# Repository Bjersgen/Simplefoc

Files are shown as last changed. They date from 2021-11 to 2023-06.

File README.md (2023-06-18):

# Simplefoc
Update 2023.3.9:

Firstly, there are some facts that need to be clarified, which I was not aware of when I initially started this project. Although the performance of these PCBs is normal at low speeds. After repeated verification, it was found that the project based on ESP32 can only reach a speed of 1000RPM when running a BLDC motor with an internal resistance of 1.5 ohms. When the speed continues to increase, the motor will exhibit symptoms such as jitter, increased current, reduced efficiency, and heat generation. This is due to several reasons working together.

1、The code of SimpleFOC platform itself has certain limitations. Because SimpleFOC is based on platforms such as Arduino, the core of the code, which is the SVPWM part, is placed in the main loop. This causes the waveform of the final output of the three phases to become stair-shaped when the speed is too high, and the processing frequency of the MCU cannot guarantee a sinusoidal waveform.

2、Do not use I2C communication for the AS5600 encoder as it is slow to trigger and has a delay, and the communication frequency has a great impact on the main loop of FOC.

3、Esp32 or Arduino itself does not have powerful features such as interrupts and DMA like stm32, and adding these functions to the underlying code of SimpleFOC is also difficult.

To address the issue of FOC being unable to run at high speeds, the following improvement solutions are recommended:

1、Change the encoder to AS5047 and use SPI or PWM, paying attention to signal integrity.

2、Use stm32 series as the main control MCU, utilize interrupts to process the SVPWM part, and trigger the interrupt every time the encoder's reading is obtained to process the direction and positioning of the magnetic field, which can greatly improve the robustness of motor control.

Feature——MAX_120W(24V*5A)——Faster(1KHZ for closed loop)

           SimpleFOC——
                            | ——BLDCmotor(self made DIY motor)
                            | ——Documents
                            | ——STM32H7_FOC
                                 |——circle(PCBs & libraries)
                            		  |——Shell(a PCB shell)
                                 |——code(using Keil5 & STM32CubeMX)
                            		  |——Inc
                            		  |——Src
                            		  |——Drivers
                            		  |——MDK-ARM
                                 |——datasheet(ICs datasheets)
                                 |——image
                                 |——readme
                            | ——pico(basic demo)                 
                            | ——pico-drv8313
                            | ——pico-drv8313 with foc
                            | ——readme

Most projects are based on Arduino, esp32-pico D4 and one project is based on stm32h743.

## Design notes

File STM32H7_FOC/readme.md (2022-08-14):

2021.12.06

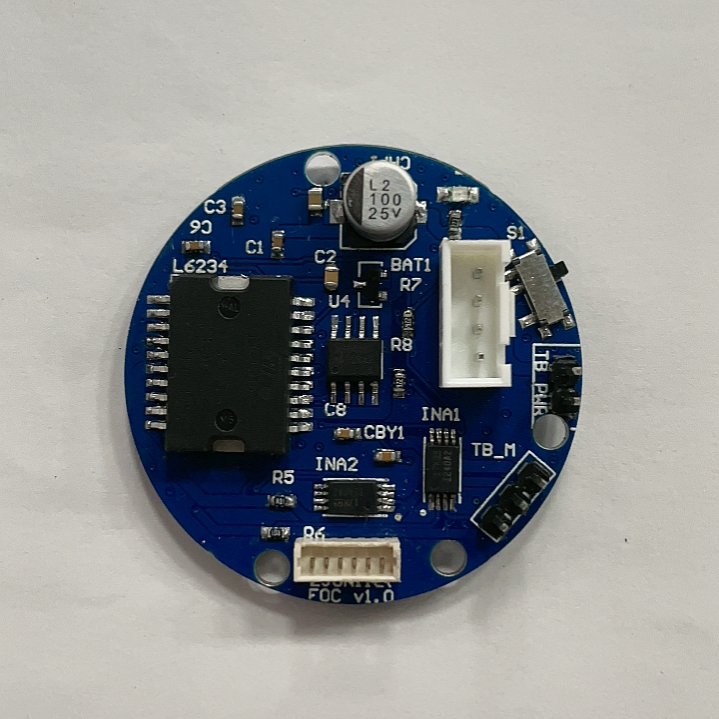
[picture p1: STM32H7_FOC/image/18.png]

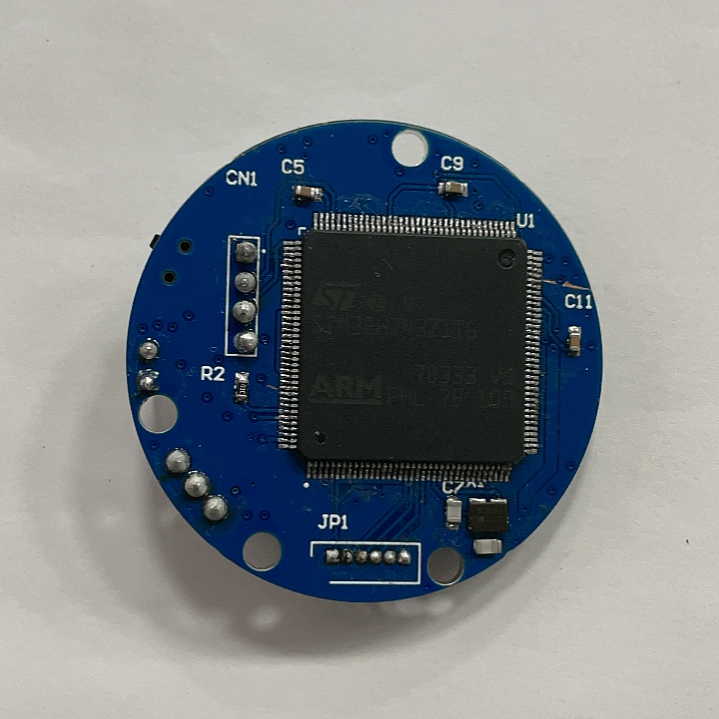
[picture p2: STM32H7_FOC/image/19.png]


基于STM32CubeMX的HAL库开发的代码

circle是基于STM32H743开发的一体化伺服系统，包括主控芯片（STM32H743）、驱动芯片、电流采样、编码器等等，对外保留了SPI接口、12-24V的供电口
以及基于SWD的调试/代码上传口、除了circle的工程外，其余的文件都是调用过的库

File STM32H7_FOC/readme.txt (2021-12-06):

2021.12.06

基于STM32CubeMX的HAL库开发的代码，目前只进行过开环测试

circle是基于STM32H743开发的一体化伺服系统，包括主控芯片（STM32H743）、驱动芯片、电流采样、编码器等等，对外保留了SPI接口、12-24V的供电口
以及基于SWD的调试/代码上传口、除了circle的工程外，其余的文件都是调用过的库

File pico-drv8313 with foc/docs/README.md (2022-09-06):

Output for 72W motor control:

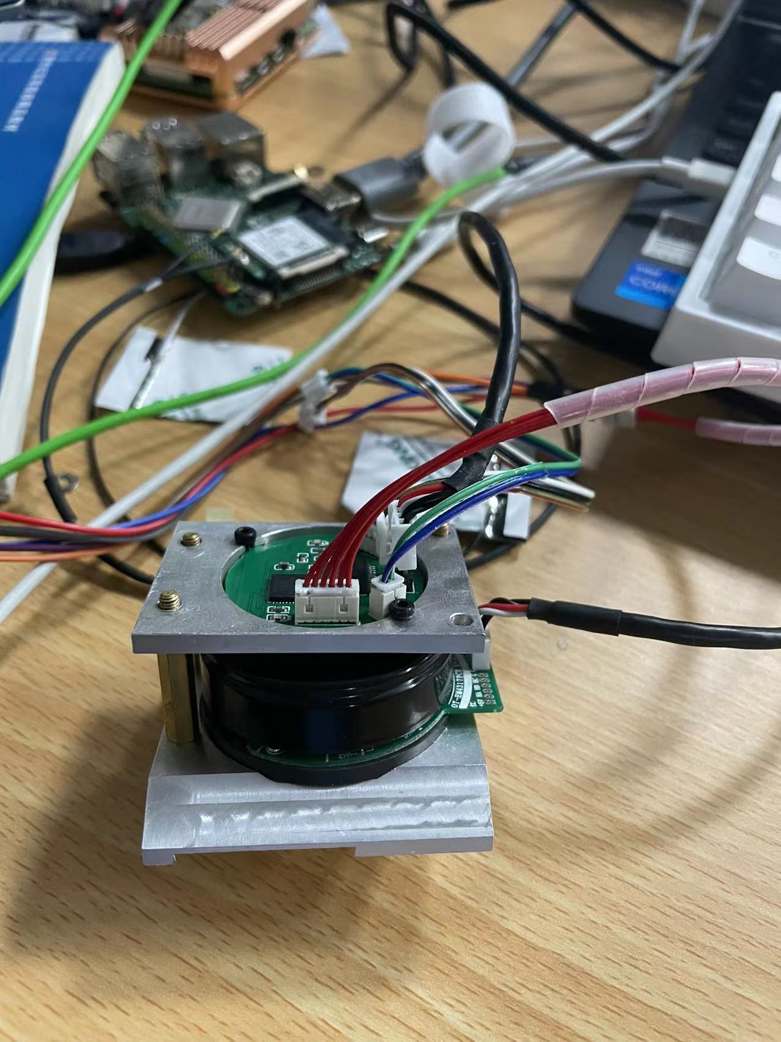
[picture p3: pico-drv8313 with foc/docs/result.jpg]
result


This directory is intended for PlatformIO Unit Testing and project tests.

Unit Testing is a software testing method by which individual units of
source code, sets of one or more MCU program modules together with associated
control data, usage procedures, and operating procedures, are tested to
determine whether they are fit for use. Unit testing finds problems early
in the development cycle.

More information about PlatformIO Unit Testing:
- https://docs.platformio.org/page/plus/unit-testing.html

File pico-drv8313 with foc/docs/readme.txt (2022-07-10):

如果是从库管理器中直接下载的SimpleFOC库需要对文件/.pio/libdeps/src/drivers/hardware_specific/esp32_mcu.cpp进行替换
文件放在该目录下，文件名为esp32_mcu.cpp

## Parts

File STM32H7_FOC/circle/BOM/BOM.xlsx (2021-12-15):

ID | Name | Designator | Footprint | Quantity | Manufacturer Part | Manufacturer | Supplier | Supplier Part | Prince
1 | 100μF | C1 | C0805 | 1
2 | 10nF | C2 | C0805 | 1
3 | 1μF | C3 | C0805 | 1
4 | 220nF | C4 | C0805 | 1
5 | 0.1μF | CBY1 | C0805 | 1
6 | 100nF | C8 | C0603 | 1
7 | 0.1μF | CL1 | C0603 | 1
8 | 1μF | C9 | C0603 | 1
9 | 100μF | CAP1 | EEH-ZA1E101XP | 1
10 | L78M08 | L1 | L7805 | 1
11 | AS5600 | U4 | SOIC8 | 1
12 | INA240A2 | INA1,INA2 | INA240 | 2
13 | STM32H743ZIT6u | U1 | LOFP100_0R5_SKT | 1
14 | Terminal connector 2pin 5mm pitch | TB_PWR | TB002-500-02BE | 1
15 | Terminal connector 3pin 5mm pitch | TB_M | 10.7MHZ | 1
16 | LED | D1 | D0805+ | 3
17 | 4 pin male header long | CN1 | HDR_1*4_2R54_V_M | 1
18 | 6 pin male header long | JP1 | HDR_1*6_2R54_V_M | 1
19 | solder_connection | SCT1 | solder_connection | 1
20 | solder_connectiong | SCT10 | solder_connection_tripple | 1
21 | 10mOhm | R5 | R/C0603 | 1
22 | 10mOhm | R6 | R/C0603 | 1
23 | 4.7KOhm | R7 | 0603R | 1
24 | 4.7KOhm | R8 | 0603R | 1

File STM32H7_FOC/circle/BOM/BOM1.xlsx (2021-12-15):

Name | Footprint | Quantity
100μF | C0805 | 5
10nF | C0805 | 5
1μF | C0805 | 5
220nF | C0805 | 5
0.1μF | C0805 | 5
100nF | C0603 | 5
0.1μF | C0603 | 5
1μF | C0603 | 5
100μF | EEH-ZA1E101XP | 5
L78M08 | L7805 | 5
AS5600 | SOIC8 | 5
INA240A2 | INA240 | 10
STM32H743ZIT6 | LOFP144_0R5_SKT | 5
Terminal connector 2pin 5mm pitch | TB002-500-02BE | 5
Terminal connector 3pin 5mm pitch | 10.7MHZ | 5
LED | D0805+ | 5
4 pin male header long | HDR_1*4_2R54_V_M | 5
6 pin male header long | HDR_1*6_2R54_V_M | 5
solder_connection | solder_connection | 5
solder_connectiong | solder_connection_tripple | 5
10mOhm | R/C0603 | 10
4.7KOhm | 0603R | 10

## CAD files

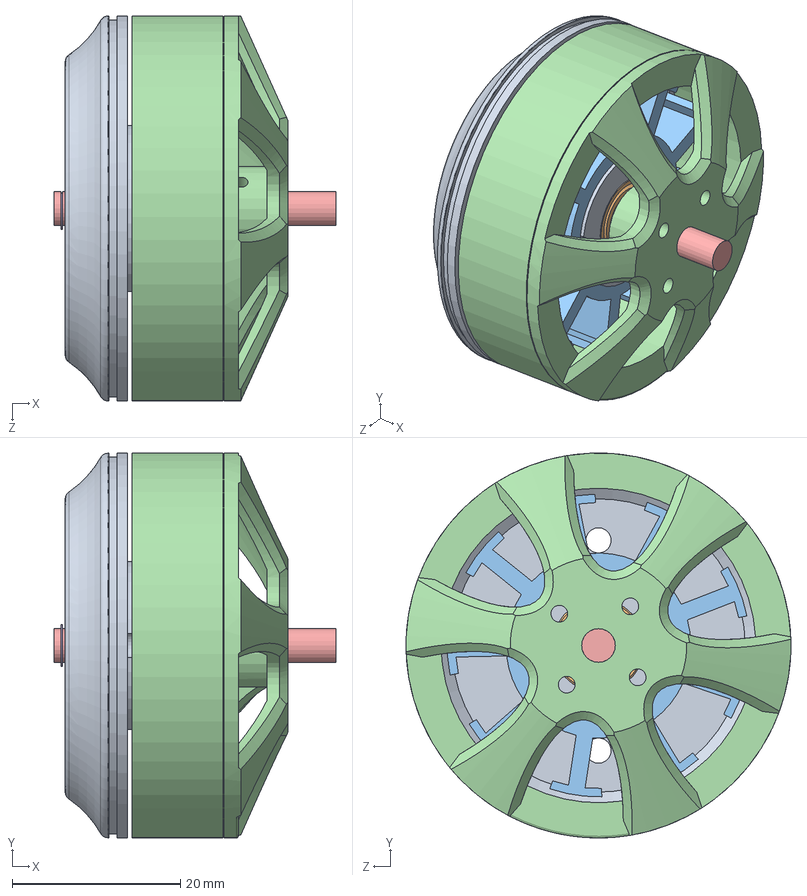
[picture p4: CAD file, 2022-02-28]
BLDCmotor/电机.SLDASM
33.5 x 45.8 x 45.8 mm
R1140ZZ bearing x 2
axle
circlip

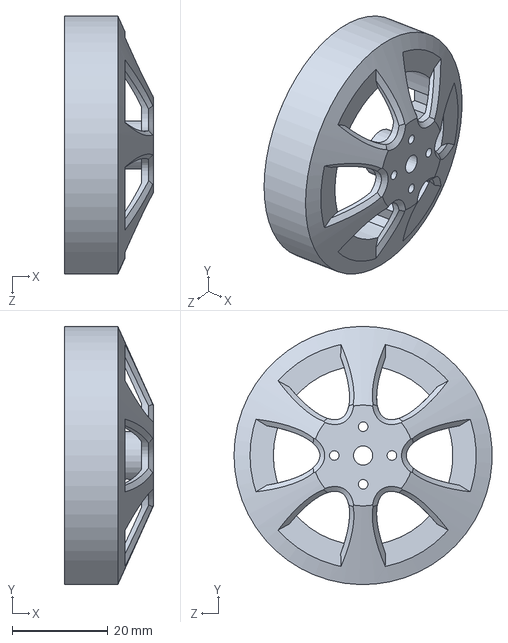
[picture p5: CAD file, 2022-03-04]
BLDCmotor/外转子.SLDPRT
18.5 x 53.8 x 53.8 mm

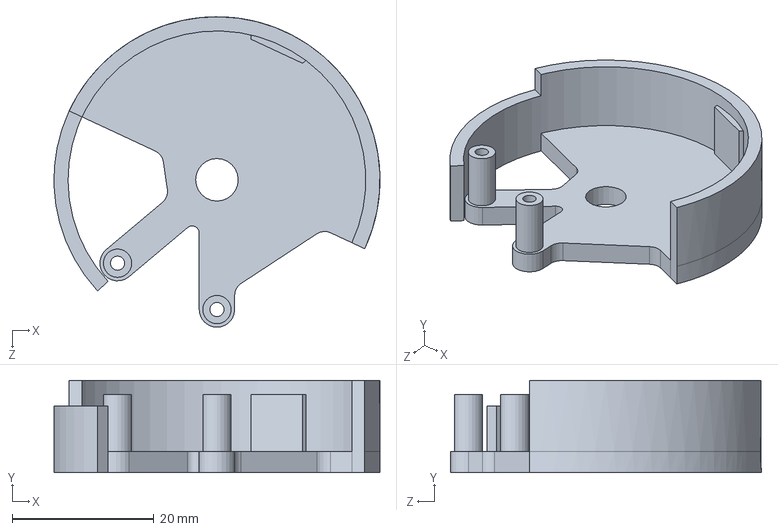
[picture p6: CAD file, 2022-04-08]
STM32H7_FOC/circle/Solidworks shell/shell.SLDPRT
46.0 x 13.0 x 43.8 mm

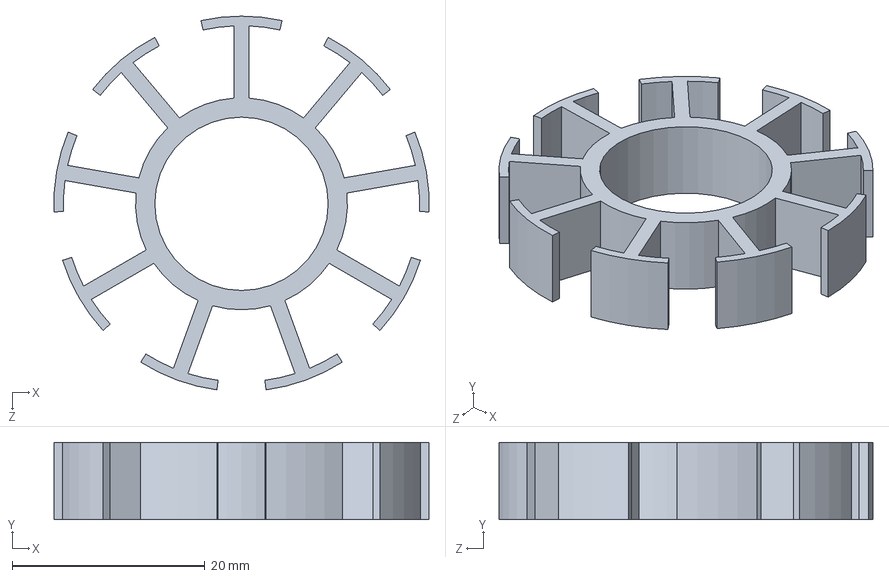
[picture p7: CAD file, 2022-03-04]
BLDCmotor/内定子.SLDPRT
38.9 x 8.00 x 38.8 mm

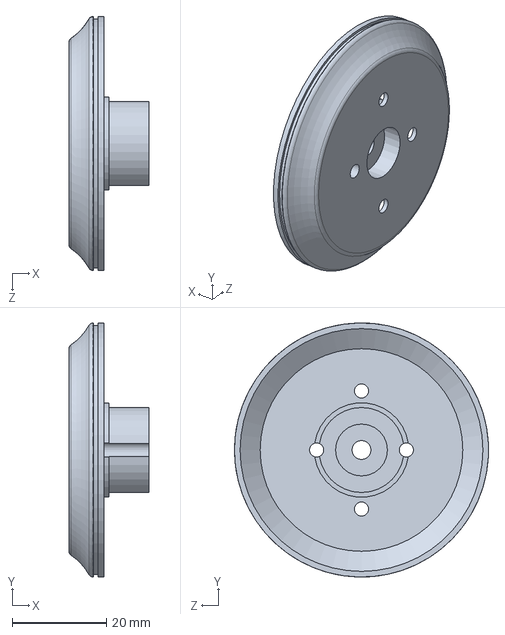
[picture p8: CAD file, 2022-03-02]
BLDCmotor/底座.SLDPRT
17.0 x 53.8 x 53.8 mm

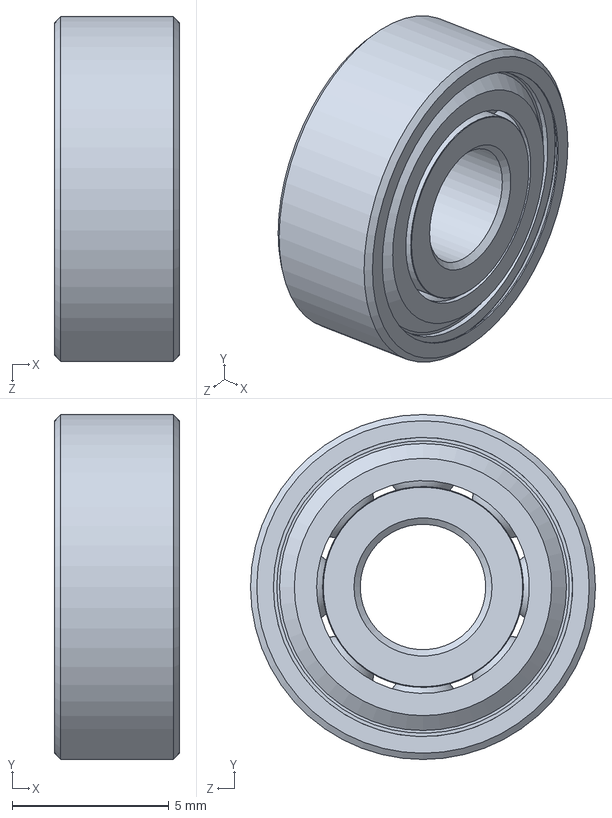
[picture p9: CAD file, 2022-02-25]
BLDCmotor/轴承.SLDPRT
4.00 x 11.0 x 11.0 mm

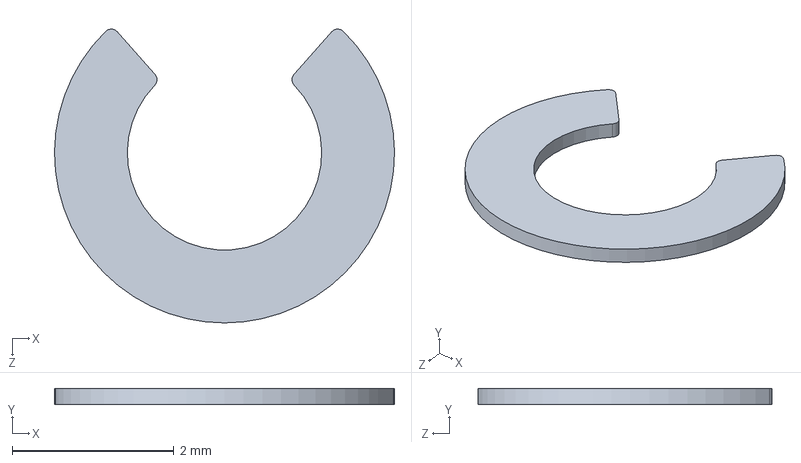
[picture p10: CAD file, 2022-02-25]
BLDCmotor/circlip.SLDPRT
4.20 x 0.2 x 3.63 mm

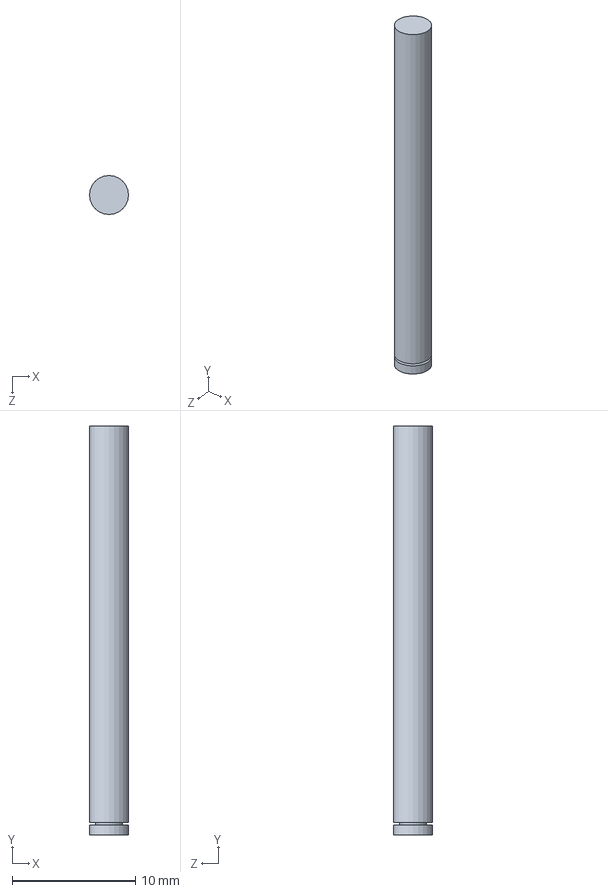
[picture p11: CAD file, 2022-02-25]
BLDCmotor/光轴.SLDPRT
3.17 x 33.2 x 3.17 mm

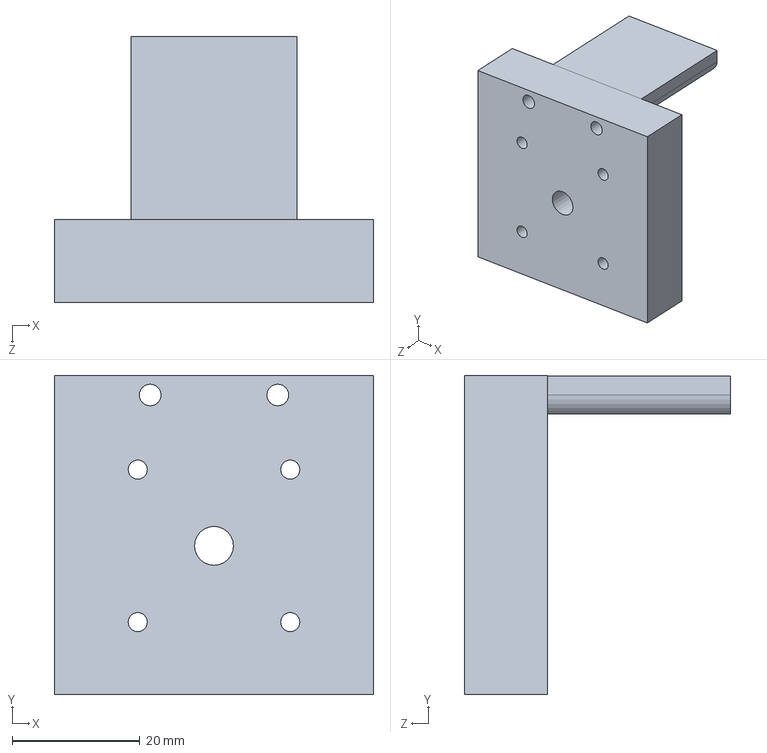
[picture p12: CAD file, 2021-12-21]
BLDCmotor/base.SLDPRT
50.0 x 50.0 x 41.7 mm

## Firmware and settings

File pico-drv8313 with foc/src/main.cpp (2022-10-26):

#include <Arduino.h>
#include <SimpleFOC.h>
#include "Wire.h"
//设置I2C设备地址，每个电机设置一个地址
#define I2C_DEV_ADDR 0x31
//电机转速
String target_velocity_string;
int target_velocity = 0;
//主机请求回复
void onRequest(){
  Wire1.print(target_velocity);
  //Serial.println("HaveRequest");
}
//收包中断，收到速度修改电机转动速度
void onReceive(int len){
  //Serial.printf("Receive[%d]: ", len);
  while(Wire1.available()){
    target_velocity_string = Wire1.read();
    target_velocity = target_velocity_string.toInt();
    if(target_velocity>=128) target_velocity = target_velocity - 256;
  }
}

//编码器采用I2C通信
MagneticSensorI2C sensor = MagneticSensorI2C(AS5600_I2C);
//电机极对数
BLDCMotor motor = BLDCMotor(8);
// BLDCDriver3PWM driver = BLDCDriver3PWM(pwmA, pwmB, pwmC, Enable(optional));
BLDCDriver3PWM driver = BLDCDriver3PWM(19, 21, 22, 23);


void setup() {
  pinMode(32, OUTPUT);
  pinMode(33, INPUT);
  pinMode(34, OUTPUT);
  digitalWrite(32,HIGH);
  digitalWrite(34,HIGH);
  Serial.begin(115200);
  //检查各个部分是否正确
  Serial.setDebugOutput(true);
  Wire1.onReceive(onReceive);
  Wire1.onRequest(onRequest);
  //与主机进行通信的I2C引脚
  Wire1.begin((uint8_t)I2C_DEV_ADDR,13,15);


  motor.useMonitoring(Serial);
  //与编码器通信的I2C引脚
  Wire.setPins(25,26);
  Wire.setClock(400000);
  sensor.init();
  motor.linkSensor(&sensor);
  //供电电压
  driver.voltage_power_supply = 16.8;
  driver.init();
  motor.linkDriver(&driver);
  motor.voltage_limit = 3;   // [V]
  motor.controller = MotionControlType::velocity;
  //PID参数
  motor.PID_velocity.P = 0.1;
  motor.PID_velocity.I = 2;
  motor.PID_velocity.D = 0;
  motor.PID_velocity.output_ramp = 1000;
  motor.LPF_velocity.Tf = 0.01;
  motor.init();
  motor.initFOC();
  motor.monitor_variables = _MON_ANGLE; // default _MON_TARGET | _MON_VOLT_Q | _MON_VEL | _MON_ANGLE
  _delay(1000);

  // #if CONFIG_IDF_TARGET_ESP32
  // char message[64];
  // snprintf(message, 64, "%u Packets.", target_velocity);
  // Wire1.slaveWrite((uint8_t *)message, strlen(message));
  // #endif
  Serial.print(1);
}

void loop() {
  //闭环速度控制
  motor.loopFOC();
  motor.move(target_velocity);
  
  if(sensor.getVelocity()>3){
    motor.voltage_limit = 16.5;
  }
  // Serial.println(target_velocity);
  // motor.monitor();
  Serial.print(sensor.getAngle());
  Serial.print("\t");
  Serial.println(sensor.getVelocity());
  Serial.print(digitalRead(33));
  
}

// #include <Arduino.h>
// #include <SimpleFOC.h>
// #include "Wire.h"
// //设置I2C设备地址，每个电机设置一个地址
// #define I2C_DEV_ADDR 0x30
// //电机转速
// String target_velocity_string;
// int target_velocity = 0;
// //主机请求回复
// void onRequest(){
//   Wire1.print(target_velocity);
//   //Serial.println("HaveRequest");
// }
// //收包中断，收到速度修改电机转动速度
// void onReceive(int len){
//   //Serial.printf("Receive[%d]: ", len);
//   while(Wire1.available()){
//     target_velocity_string = Wire1.read();
//     target_velocity = target_velocity_string.toInt();
//     if(target_velocity>=128) target_velocity = target_velocity - 256;
//   }
// }
// //电机极对数
// BLDCMotor motor = BLDCMotor(8);
// // BLDCDriver3PWM driver = BLDCDriver3PWM(pwmA, pwmB, pwmC, Enable(optional));
// BLDCDriver3PWM driver = BLDCDriver3PWM(19, 21, 22, 23);


// void setup() {

//   pinMode(32, OUTPUT);
//   pinMode(33, INPUT);
//   pinMode(34, OUTPUT);
//   digitalWrite(32,HIGH);
//   digitalWrite(34,HIGH);
//   Serial.begin(115200);
//   //检查各个部分是否正确
//   Serial.setDebugOutput(true);
//   Wire1.onReceive(onReceive);
//   Wire1.onRequest(onRequest);
//   //与主机进行通信的I2C引脚
//   Wire1.begin((uint8_t)I2C_DEV_ADDR,13,15);


//   motor.useMonitoring(Serial);
//   //与编码器通信的I2C引脚
//   Wire.setPins(25,26);
//   Wire.setClock(400000);
//   //供电电压
//   driver.voltage_power_supply = 16.8;
//   driver.init();
//   motor.linkDriver(&driver);
//   motor.voltage_limit = 3;   // [V]
//   motor.controller = MotionControlType::velocity_openloop;

//   motor.init();
//   motor.monitor_variables = _MON_ANGLE; // default _MON_TARGET | _MON_VOLT_Q | _MON_VEL | _MON_ANGLE
//   _delay(1000);

//   // #if CONFIG_IDF_TARGET_ESP32
//   // char message[64];
//   // snprintf(message, 64, "%u Packets.", target_velocity);
//   // Wire1.slaveWrite((uint8_t *)message, strlen(message));
//   // #endif
//   Serial.print(1);
// }

// void loop() {
//   //闭环速度控制
//   motor.move(target_velocity);
  
//   // Serial.println(target_velocity);
//   // motor.monitor();
//   Serial.print(digitalRead(33));
  
// }

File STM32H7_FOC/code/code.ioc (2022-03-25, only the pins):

Mcu.UserName=STM32H743ZITx
PA1.GPIO_Label=RMII_REF_CLK
PA1.Signal=ETH_REF_CLK
PA10.GPIO_Label=USB_ID
PA10.Signal=USB_OTG_FS_ID
PA11.GPIO_Label=USB_DM
PA11.Signal=USB_OTG_FS_DM
PA12.GPIO_Label=USB_DP
PA12.Signal=USB_OTG_FS_DP
PA2.GPIO_Label=RMII_MDIO
PA2.Signal=ETH_MDIO
PA3.Signal=USART2_RX
PA7.GPIO_Label=RMII_CRS_DV
PA7.Signal=ETH_CRS_DV
PA8.GPIO_Label=USB_SOF [TP1]
PA8.Signal=USB_OTG_FS_SOF
PA9.GPIO_Label=USB_VBUS
PA9.Signal=USB_OTG_FS_VBUS
PB13.GPIO_Label=RMII_TXD1
PB13.Signal=ETH_TXD1
PB14.GPIO_Label=LD3 [Red]
PB14.Signal=GPIO_Output
PB7.GPIO_Label=LD2 [Blue]
PB7.Signal=GPIO_Output
PC1.GPIO_Label=RMII_MDC
PC1.Signal=ETH_MDC
PC13.GPIO_Label=USER_Btn [B1]
PC13.Signal=GPXTI13
PC4.GPIO_Label=RMII_RXD0
PC4.Signal=ETH_RXD0
PC5.GPIO_Label=RMII_RXD1
PC5.Signal=ETH_RXD1
PD5.Signal=USART2_TX
PD8.GPIO_Label=STLK_RX [STM32F103CBT6_PA3]
PD8.Signal=USART3_TX
PD9.GPIO_Label=STLK_TX [STM32F103CBT6_PA2]
PD9.Signal=USART3_RX
PE11.Signal=S_TIM1_CH2
PE13.Signal=S_TIM1_CH3
PE9.Signal=S_TIM1_CH1
PG11.GPIO_Label=RMII_TX_EN
PG11.Signal=ETH_TX_EN
PG13.GPIO_Label=RMII_TXD0
PG13.Signal=ETH_TXD0
PG6.GPIO_Label=USB_PowerSwitchOn [STMPS2151STR_EN]
PG6.Signal=GPIO_Output
PG7.GPIO_Label=USB_OverCurrent [STMPS2151STR_FAULT]
PG7.Signal=GPIO_Input

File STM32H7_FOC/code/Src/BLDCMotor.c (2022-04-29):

#include "MyProject.h"
#include "stdio.h"



/******************************************************************************/
extern float target;
/******************************************************************************/
long sensor_direction;
float voltage_power_supply;
float voltage_limit;
float voltage_sensor_align;
int  pole_pairs;
unsigned long open_loop_timestamp;
float velocity_limit;
float current_limit;
/******************************************************************************/
int alignSensor(void);
float velocityOpenloop(float target_velocity);
float angleOpenloop(float target_angle);

/******************************************************************************/
void Motor_init(void)
{
	printf("MOT: Init\r\n");
	
//	new_voltage_limit = current_limit * phase_resistance;
//	voltage_limit = new_voltage_limit < voltage_limit ? new_voltage_limit : voltage_limit;
	if(voltage_sensor_align > voltage_limit) voltage_sensor_align = voltage_limit;
	
	pole_pairs=7;
	sensor_direction=UNKNOWN;
	
	M1_Enable;
	printf("MOT: Enable driver.\r\n");
}

void Motor_initFOC(void)
{
	alignSensor();    
	
	//added the shaft_angle update
	//angle_prev=getAngle();  //getVelocity(),make sure velocity=0 after power on
	HAL_Delay(50);
	shaft_velocity = shaftVelocity();  //
	HAL_Delay(5);
	shaft_angle = shaftAngle();// shaft angle
	if(controller==Type_angle)target=shaft_angle;//
	
	HAL_Delay(200);
}

int alignSensor(void)
{
	long i;
	float angle;
	float mid_angle,end_angle;
	float moved;
	
	printf("MOT: Align sensor.\r\n");
	
	// find natural direction
	// move one electrical revolution forward
	for(i=0; i<=500; i++)
	{
		angle = _3PI_2 + _2PI * i / 500.0;
		setPhaseVoltage(voltage_sensor_align, 0,  angle);
		HAL_Delay(2);
	}
	mid_angle=getAngle();
	
	for(i=500; i>=0; i--) 
	{
		angle = _3PI_2 + _2PI * i / 500.0 ;
		setPhaseVoltage(voltage_sensor_align, 0,  angle);
		HAL_Delay(2);
	}
	end_angle=getAngle();
	setPhaseVoltage(0, 0, 0);
	HAL_Delay(200);
	
	printf("mid_angle=%.4f\r\n",mid_angle);
	printf("end_angle=%.4f\r\n",end_angle);
	
	moved =  fabs(mid_angle - end_angle);
	if((mid_angle == end_angle)||(moved < 0.01))  //?????????
	{
		printf("MOT: Failed to notice movement loop222.\r\n");
		M1_Disable;    //???????,????
		return 0;
	}
	else if(mid_angle < end_angle)
	{
		printf("MOT: sensor_direction==CCW\r\n");
		sensor_direction=CCW;
	}
	else
	{
		printf("MOT: sensor_direction==CW\r\n");
		sensor_direction=CW;
	}
	
	
	printf("MOT: PP check: ");    //??Pole_Pairs
	if( fabs(moved*pole_pairs - _2PI) > 0.5 )  // 0.5 is arbitrary number it can be lower or higher!
	{
		printf("fail - estimated pp:");
		pole_pairs=_2PI/moved+0.5;     //??????,????
		printf("%d\r\n",pole_pairs);
  }
	else
		printf("OK!\r\n");
	
	
	setPhaseVoltage(voltage_sensor_align, 0,  _3PI_2);  //????????
	HAL_Delay(700);
	zero_electric_angle = _normalizeAngle(_electricalAngle(sensor_direction*getAngle(), pole_pairs));
	HAL_Delay(20);
	printf("MOT: Zero elec. angle:");
	printf("%.4f\r\n",zero_electric_angle);
	
	setPhaseVoltage(0, 0, 0);
	HAL_Delay(200);
	
	return 1;
}
void loopFOC(void)
{
	if( controller==Type_angle_openloop || controller==Type_velocity_openloop ) return;
	
	shaft_angle = shaftAngle();// shaft angle
	electrical_angle = electricalAngle();// electrical angle - need shaftAngle to be called first
	
	switch(torque_controller)
	{
		case Type_voltage:  // no need to do anything really
			break;
		case Type_dc_current:
			// read overall current magnitude
      current.q = getDCCurrent(electrical_angle);
      // filter the value values
      current.q = LPF_current_q(current.q);
      // calculate the phase voltage
      voltage.q = PID_current_q(current_sp - current.q); 
      voltage.d = 0;
			break;
		case Type_foc_current:
			// read dq currents
      current = getFOCCurrents(electrical_angle);
      // filter values
      current.q = LPF_current_q(current.q);
      current.d = LPF_current_d(current.d);
      // calculate the phase voltages
      voltage.q = PID_current_q(current_sp - current.q); 
      voltage.d = PID_current_d(-current.d);
			break;
		default:
			printf("MOT: no torque control selected!");
			break;
	}
	// set the phase voltage - FOC heart function :)
  setPhaseVoltage(voltage.q, voltage.d, electrical_angle);
}
void move(float new_target)
{
	shaft_velocity = shaftVelocity();
	
	switch(controller)
	{
		case Type_torque:
			if(torque_controller==Type_voltage)voltage.q = new_target;  // if voltage torque control
		  else
				current_sp = new_target; // if current/foc_current torque control
			break;
		case Type_angle:
			// angle set point
      shaft_angle_sp = new_target;
      // calculate velocity set point
      shaft_velocity_sp = PID_angle( shaft_angle_sp - shaft_angle );
      // calculate the torque command
      current_sp = PID_velocity(shaft_velocity_sp - shaft_velocity); // if voltage torque control
      // if torque controlled through voltage  
      if(torque_controller == Type_voltage)
			{
				voltage.q = current_sp;
        voltage.d = 0;
      }
			break;
		case Type_velocity:
			// velocity set point
      shaft_velocity_sp = new_target;
      // calculate the torque command
      current_sp = PID_velocity(shaft_velocity_sp - shaft_velocity); // if current/foc_current torque control
      // if torque controlled through voltage control 
      if(torque_controller == Type_voltage)
			{
        voltage.q = current_sp;  // use voltage if phase-resistance not provided
        voltage.d = 0;
      }
			break;
		case Type_velocity_openloop:
			// velocity control in open loop
      shaft_velocity_sp = new_target;
      voltage.q = velocityOpenloop(shaft_velocity_sp); // returns the voltage that is set to the motor
      voltage.d = 0;
			break;
		case Type_angle_openloop:
			// angle control in open loop
      shaft_angle_sp = new_target;
      voltage.q = angleOpenloop(shaft_angle_sp); // returns the voltage that is set to the motor
      voltage.d = 0;
			break;
	}
	if((current_limit>0)&&((torque_controller == Type_dc_current)||(torque_controller == Type_foc_current)))
	{
		if(current_sp> current_limit)current_sp = current_limit;  //????
		if(current_sp<-current_limit)current_sp =-current_limit;
	}
}
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

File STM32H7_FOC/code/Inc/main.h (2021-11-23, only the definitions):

#define USER_Btn_Pin GPIO_PIN_13
#define USER_Btn_GPIO_Port GPIOC
#define MCO_Pin GPIO_PIN_0
#define MCO_GPIO_Port GPIOH
#define RMII_MDC_Pin GPIO_PIN_1
#define RMII_MDC_GPIO_Port GPIOC
#define RMII_REF_CLK_Pin GPIO_PIN_1
#define RMII_REF_CLK_GPIO_Port GPIOA
#define RMII_MDIO_Pin GPIO_PIN_2
#define RMII_MDIO_GPIO_Port GPIOA
#define RMII_CRS_DV_Pin GPIO_PIN_7
#define RMII_CRS_DV_GPIO_Port GPIOA
#define RMII_RXD0_Pin GPIO_PIN_4
#define RMII_RXD0_GPIO_Port GPIOC
#define RMII_RXD1_Pin GPIO_PIN_5
#define RMII_RXD1_GPIO_Port GPIOC
#define RMII_TXD1_Pin GPIO_PIN_13
#define RMII_TXD1_GPIO_Port GPIOB
#define LD3_Pin GPIO_PIN_14
#define LD3_GPIO_Port GPIOB
#define STLK_RX_Pin GPIO_PIN_8
#define STLK_RX_GPIO_Port GPIOD
#define STLK_TX_Pin GPIO_PIN_9
#define STLK_TX_GPIO_Port GPIOD
#define USB_PowerSwitchOn_Pin GPIO_PIN_6
#define USB_PowerSwitchOn_GPIO_Port GPIOG
#define USB_OverCurrent_Pin GPIO_PIN_7
#define USB_OverCurrent_GPIO_Port GPIOG
#define USB_SOF_Pin GPIO_PIN_8
#define USB_SOF_GPIO_Port GPIOA
#define USB_VBUS_Pin GPIO_PIN_9
#define USB_VBUS_GPIO_Port GPIOA
#define USB_ID_Pin GPIO_PIN_10
#define USB_ID_GPIO_Port GPIOA
#define USB_DM_Pin GPIO_PIN_11
#define USB_DM_GPIO_Port GPIOA
#define USB_DP_Pin GPIO_PIN_12
#define USB_DP_GPIO_Port GPIOA
#define RMII_TX_EN_Pin GPIO_PIN_11
#define RMII_TX_EN_GPIO_Port GPIOG
#define RMII_TXD0_Pin GPIO_PIN_13
#define RMII_TXD0_GPIO_Port GPIOG
#define LD2_Pin GPIO_PIN_7
#define LD2_GPIO_Port GPIOB

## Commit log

2021-11-07 Arduino source
2022-04-07 change footprint
    [circle.PrjPCB]
2022-04-07 PCB shell
    [circle - 副本.SchDoc, shell.SLDPRT]
2022-04-08 perfect the code
    [shell.SLDPRT]
2022-08-11 4 layers PCB
    [4.PcbDoc, pico.PrjPCB]
2022-08-14 add 4 layer pcb
    [4.PcbDoc, new.pcbdoc, pico.PrjPCB]
2022-10-26 add another version
    [4.PcbDoc, Main SCH.schdoc, Main_2022-10-17.pcbdoc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]

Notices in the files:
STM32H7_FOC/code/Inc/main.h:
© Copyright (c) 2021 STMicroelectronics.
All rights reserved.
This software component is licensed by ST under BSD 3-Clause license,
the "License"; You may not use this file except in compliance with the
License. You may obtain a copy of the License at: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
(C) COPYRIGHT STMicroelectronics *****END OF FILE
